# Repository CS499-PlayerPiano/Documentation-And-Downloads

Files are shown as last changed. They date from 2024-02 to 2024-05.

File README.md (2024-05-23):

# Documentation and Downloads
Here you will find misc files and documentation for the piano.

- [Documentation and Downloads](#documentation-and-downloads)
  - [Presentation & Writeup](#presentation--writeup)
  - [3D Models](#3d-models)
  - [Electronics \& Schematics](#electronics--schematics)
  - [Code and Runtime](#code-and-runtime)

## [Presentation & Writeup](./Presentation%20and%20Writeup/)
This folder contains the presentations and writeups for our projects.
* [Final Presentation Video](https://www.youtube.com/watch?v=wYrI8wo7iek)
* [Final Writeup (PDF)](./Presentation%20and%20Writeup/Player%20Piano%20Final%20Report.pdf)
* [Presentation (PDF)](./Presentation%20and%20Writeup/Player%20Piano.pdf)
* [Presentation (PPTX)](./Presentation%20and%20Writeup/Player%20Piano.pptx)

## [3D Models](./3D%20Models/README.md)
This folder contains the 3D models for the piano. The models are in `.stl` format and can be viewed in any 3D modeling software. There are also `.f3z` files which are the original files for the 3D models in the Fusion 360 software.

## [Electronics & Schematics](./Electronics%20and%20Schematics/README.md)
This folder contains the schematics for the piano, and the PCB design files.
* [V1.0](./Electronics%20and%20Schematics/v1.0/)
* [V1.1](./Electronics%20and%20Schematics/v1.1/)

## [Code and Runtime](./Code%20and%20Runtime/)
This folder contains info how to run and configure the various programs that run the piano.
* [Running the piano program(s)](./Code%20and%20Runtime/Running.md)
* [Configuration](./Code%20and%20Runtime/Configuration.md)

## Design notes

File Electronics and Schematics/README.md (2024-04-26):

# Electronic and Schematics
This folder contains the schematics for the piano, and the PCB design files.

- [Electronic and Schematics](#electronic-and-schematics)
  - [Schematic and PCB Design](#schematic-and-pcb-design)
    - [Version 1.0](#version-10)
    - [Version 1.1](#version-11)

## Schematic and PCB Design
### Version 1.0
* [EasyEDA Schematic](./v1.0/SCH_PLU-Piano-v1.0_2024-04-26.json)
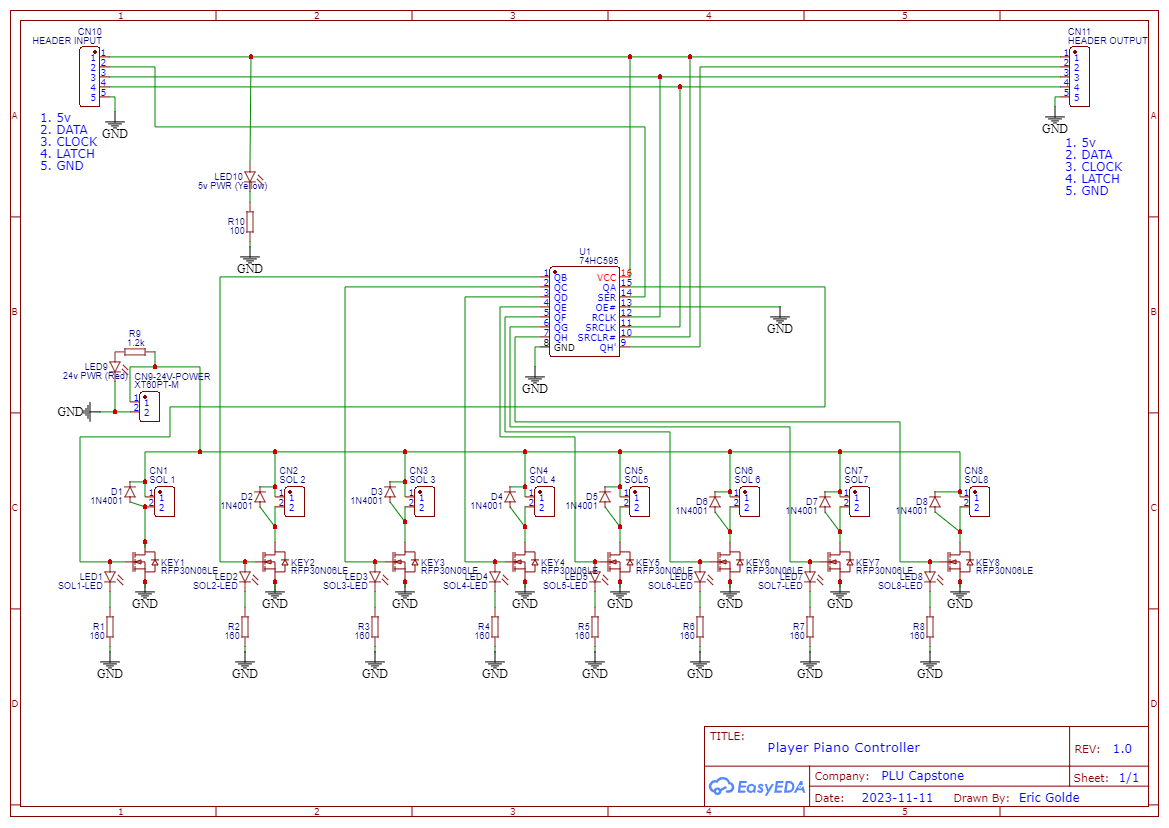
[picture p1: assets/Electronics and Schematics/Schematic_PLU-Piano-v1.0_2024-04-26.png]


* [Gerber Files](./v1.0/Gerber_PLU-Piano-v1.0_PCB_PLU-Piano-v1.0_2024-04-26.zip)
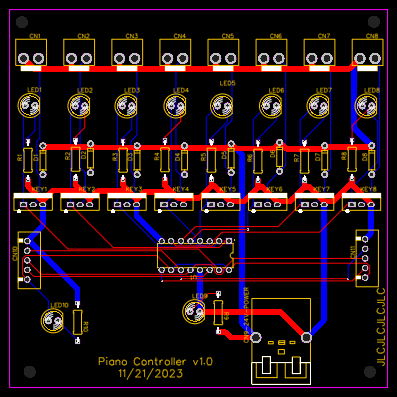
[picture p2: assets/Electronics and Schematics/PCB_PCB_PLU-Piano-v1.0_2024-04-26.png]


* [BOM](./v1.0/BOM_PLU-Piano-v1.0_2024-04-26.csv)

### Version 1.1
* [EasyEDA Schematic](./v1.1/SCH_PLU-Piano-v1.1_2024-04-26.json)
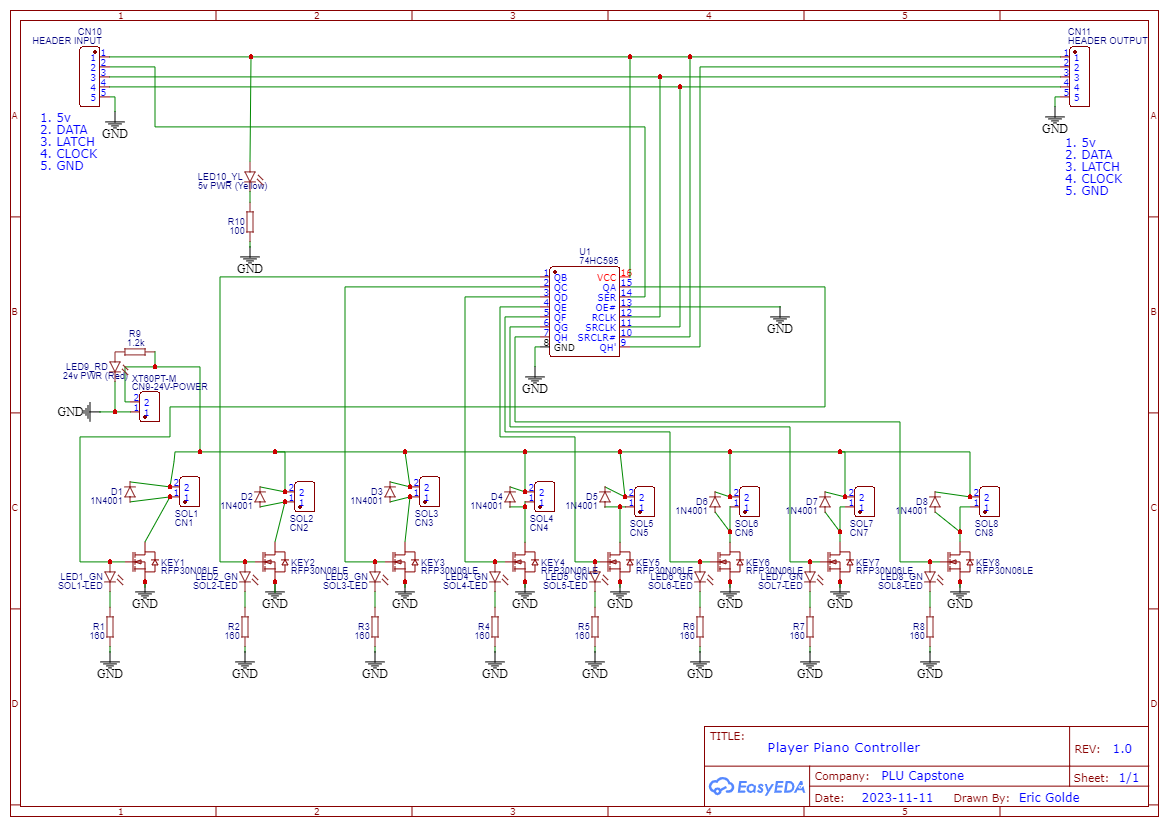
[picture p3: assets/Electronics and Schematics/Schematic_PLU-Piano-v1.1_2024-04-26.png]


* [Gerber Files](./v1.1/Gerber_PLU-Piano-v1.1_PCB_PLU-Piano-v1.1_2024-04-26.zip)
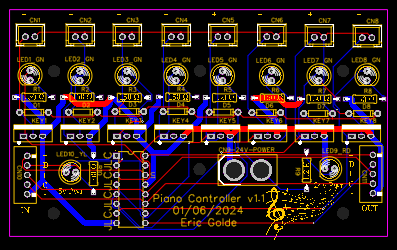
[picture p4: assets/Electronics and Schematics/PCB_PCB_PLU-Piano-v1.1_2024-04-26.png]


* [BOM](./v1.1/BOM_PLU-Piano-v1.1_2024-04-26.csv)

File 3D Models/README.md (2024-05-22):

## 3D Models
### [Solenoid Holder](./Solenoid%20holder/)
Settings:
- Perimeters: 6
- Infill: 25%
- 0.2mm layer height
- PETG

Files:
- [SolenoidHolder2 v13.f3d](./Solenoid%20holder/SolenoidHolder2%20v13.f3d) - Main tileable solenoid holder
- [SolenoidHolder2 v13.stl](./Solenoid%20holder/SolenoidHolder2%20v13.stl) Main tileable solenoid holder
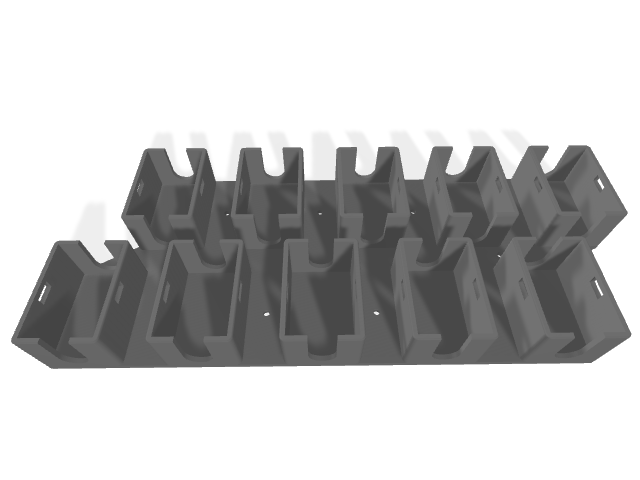
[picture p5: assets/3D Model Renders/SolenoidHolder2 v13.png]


- [LeftWhiteKeyFrame.stl](./Solenoid%20holder/LeftWhiteKeyFrame.stl) - 7 keys for the left end
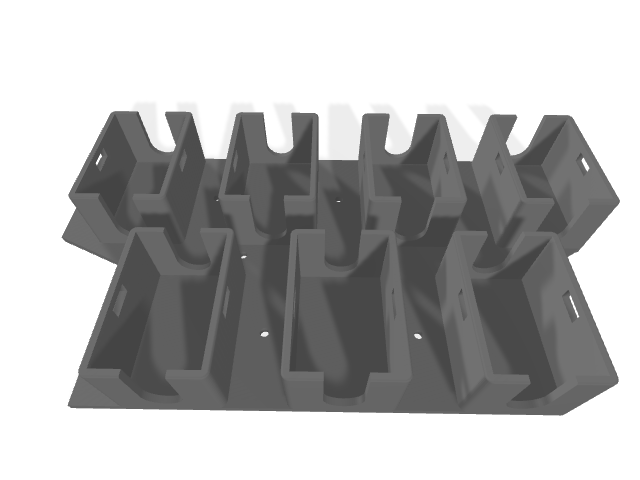
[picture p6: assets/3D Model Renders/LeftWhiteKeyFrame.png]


- [RightWhiteKeyFrame.stl](/Solenoid%20holder/RightWhiteKeyFrame.stl) - 5 keys for the right end
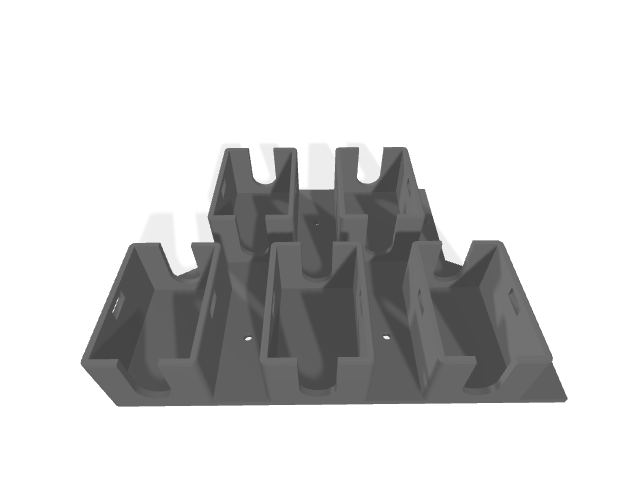
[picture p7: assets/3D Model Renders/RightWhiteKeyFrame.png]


### [Threaded Rod Connectors](./Threaded%20Rod%20Connectors/)
Settings:
- Perimeters: 3
- Infill: 25%
- 0.2mm layer height
- PETG

Files:
- [ThreadedRodConnectors v12.f3d](./Threaded%20Rod%20Connectors/ThreadedRodConnectors%20v12.f3d) - Connects the solenoid to the threaded rod
- [SolenoidToRodAttachment.stl](./Threaded%20Rod%20Connectors/SolenoidToRodAttachment.stl) - Connects the solenoid to the threaded rod
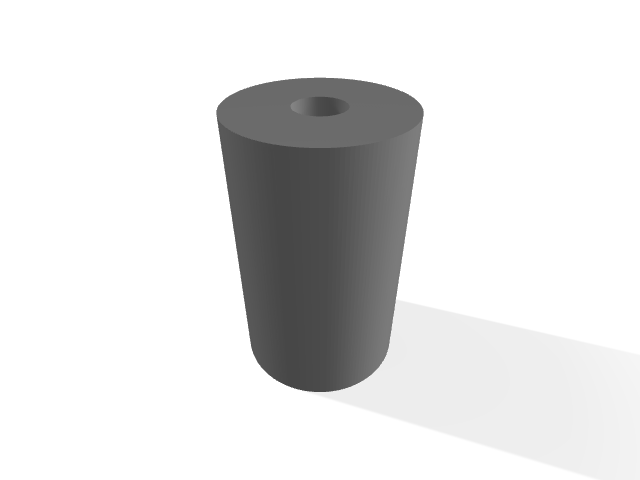
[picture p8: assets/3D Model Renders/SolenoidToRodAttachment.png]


- [Striker](./Threaded%20Rod%20Connectors/Striker.stl) - Connects the threaded rod to hit the keys
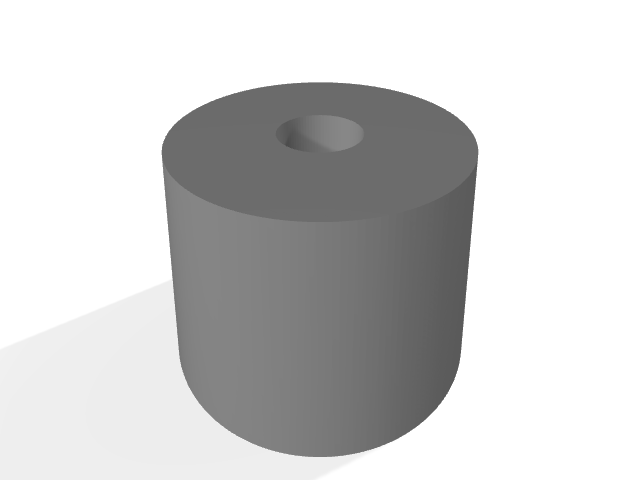
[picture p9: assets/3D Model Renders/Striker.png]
Striker


- [Power Strip Bracket](./PowerStripBracket.stl)
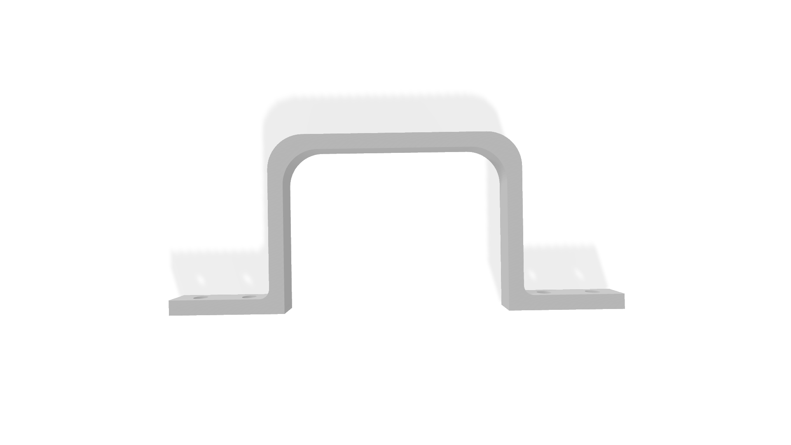
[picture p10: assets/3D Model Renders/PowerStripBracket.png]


- [Power Supply Mount](./Power%20Supply/)
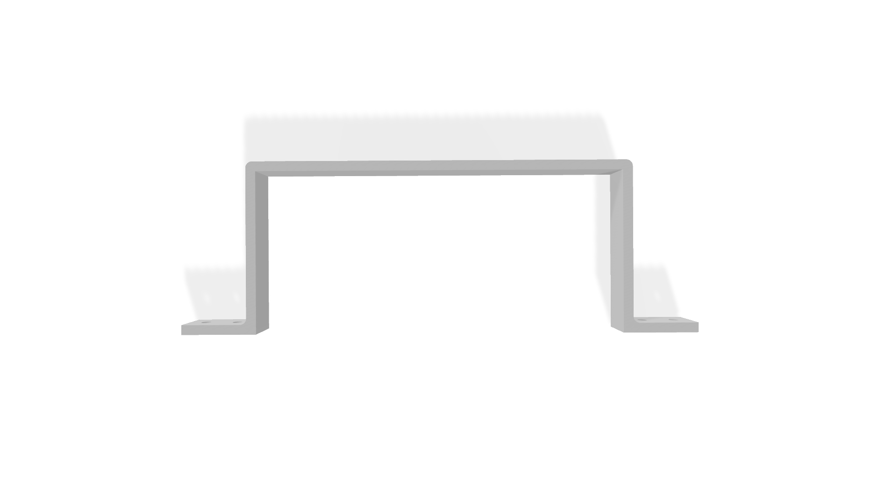
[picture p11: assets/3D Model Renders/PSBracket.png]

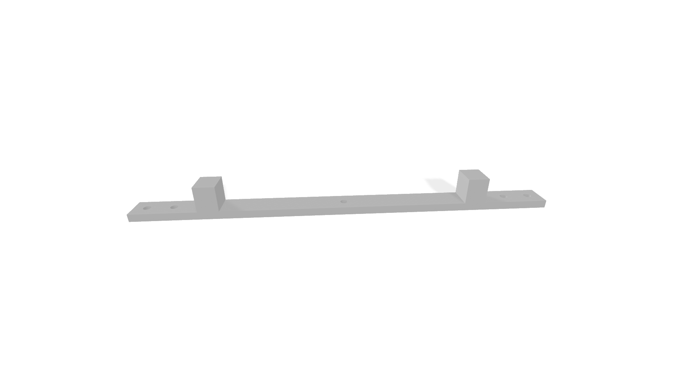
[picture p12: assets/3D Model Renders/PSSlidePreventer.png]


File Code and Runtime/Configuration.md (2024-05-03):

# Configuration

## Outputs.json
```json5
{
    // Configuration for the Logger output
    "Logger": {
        "enabled": true
    },

    // Configuration for the Midi Synthesizer
    "Midi Synthesizer": {
        "enabled": true
    },

    // Configuration for the Virtual Piano GUI
    "Virtual Piano GUI": {
        "enabled": true,

        // Either "RAINBOW_GRADIENT" or "TRACK_NUMBER"
        "colorMode": "RAINBOW_GRADIENT"
    },

    // Configuration for the Synthesia Viewer (Not yet implemented)
    "Synthesia Viewer": {
        "enabled": false
    },

    // Configuration for the web server
    "Javalin Web Server": {

        // Port to run the web server on
        "port": 8898,

        // Interval in milliseconds to send timestamp updates to the client
        "timestampInterval": 500
    },

    // Configuration for the Physical Piano
    "Arduino": {
        "enabled": true,

        // COM port for the Arduino
        "comPort": "COM7",

        // Baud rate for the Arduino
        "baudRate": 115200,

        // Should we print debug output if the Arduino sends it?
        "printDebugOutputFromArduino": true,

        // Should we send a power reset after every song?
        "sendPowerResetAfterEverySong": true,

        // Shoud we ignore velocity, and only send 255 or 0?
        "ignoreVelocity": false,

        // Velocity mapping for energising the solenoids.
        // The solenoids stop responding at 120, and are fully energised at 255.
        "velocityMapping": {
            "min": 120,
            "max": 255
        },

        // Mapping of the notes to the solenoids
        // Physical Key Index -> Midi Note
        // 0 is the lowest key, 87 is the highest key
        "noteMapping": {
            "0": 101,
            "1": 102,
            "2": 103,
            "3": 104,
            "4": 105,
            "5": 106,
            "6": 107,
            "7": 108,
            "8": 93,
            "9": 94,
            "10": 95,
            "11": 96,
            "12": 97,
            "13": 98,
            "14": 99,
            "15": 100,
            "16": 85,
            "17": 86,
            "18": 87,
            "19": 88,
            "20": 89,
            "21": 90,
            "22": 91,
            "23": 92,
            "24": 77,
            "25": 78,
            "26": 79,
            "27": 80,
            "28": 81,
            "29": 82,
            "30": 83,
            "31": 84,
            "32": 69,
            "33": 70,
            "34": 71,
            "35": 72,
            "36": 73,
            "37": 74,
            "38": 75,
            "39": 76,
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
        }
    }
}
```

## Programs.json
```json5
{
    // Configuration for the Midi Keyboard Input
    "midi-keyboard": {
        // Should we print all the device names on boot?
        "printAllDeviceNames": true,

        // Name of the device to use
        "deviceName": "AKM320",

        // Should we ignore velocity when reading the midi input?
        "ignoreVelocity": true
    }
}
```

## TODO Configs:
We ran out of time to make these configurable, but they should be configurable in the future.
```
plu.capstone.playerpiano.sheetmusic.cleaner.steps.Step4OffsetNoteTimes LN: 28-120. timeToRelease(), timeToHit(), calcShiftForwardAmount()
```

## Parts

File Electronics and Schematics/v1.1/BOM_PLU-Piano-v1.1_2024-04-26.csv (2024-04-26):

ID | Name | Designator | Footprint | Quantity | Manufacturer Part | Manufacturer | Supplier | Supplier Part | Price | Pins | 3DModel | Contributor | JLCPCB Part Class | description | link
1 | 24v PWR (Red) | LED9_RD | LED5MM | 1 |  |  |  |  |  | 2 | LED-TH-5MM_RED COPY | SparkFun
2 | SOL1-LED | LED1_GN | LED5MM | 1 |  |  |  |  |  | 2 | LED-TH-5MM_G COPY | SparkFun
3 | SOL2-LED | LED2_GN | LED5MM | 1 |  |  |  |  |  | 2 | LED-TH-5MM_G COPY | SparkFun
4 | SOL3-LED | LED3_GN | LED5MM | 1 |  |  |  |  |  | 2 | LED-TH-5MM_G COPY | SparkFun
5 | SOL4-LED | LED4_GN | LED5MM | 1 |  |  |  |  |  | 2 | LED-TH-5MM_G COPY | SparkFun
6 | SOL5-LED | LED5_GN | LED5MM | 1 |  |  |  |  |  | 2 | LED-TH-5MM_G COPY | SparkFun
7 | SOL6-LED | LED6_GN | LED5MM | 1 |  |  |  |  |  | 2 | LED-TH-5MM_G COPY | SparkFun
8 | SOL7-LED | LED7_GN | LED5MM | 1 |  |  |  |  |  | 2 | LED-TH-5MM_G COPY | SparkFun
9 | SOL8-LED | LED8_GN | LED5MM | 1 |  |  |  |  |  | 2 | LED-TH-5MM_G COPY | SparkFun
10 | 5v PWR (Yellow) | LED10_YL | LED5MM | 1 |  |  |  |  |  | 2 | LED-TH_5MM_YELLOW-GREEN | SparkFun
11 | SOL1 | CN1 | CONN-TH_XH-2A | 1 | XH-2A | 韩国韩荣 | LCSC | C2910525 | 0.043 | 2 | XH2.5-2A | LCSC | Extended Part |  | https://item.szlcsc.com/20789.html
12 | SOL2 | CN2 | CONN-TH_XH-2A | 1 | XH-2A | 韩国韩荣 | LCSC | C2910525 | 0.043 | 2 | XH2.5-2A | LCSC | Extended Part |  | https://item.szlcsc.com/20789.html
13 | SOL3 | CN3 | CONN-TH_XH-2A | 1 | XH-2A | 韩国韩荣 | LCSC | C2910525 | 0.043 | 2 | XH2.5-2A | LCSC | Extended Part |  | https://item.szlcsc.com/20789.html
14 | SOL4 | CN4 | CONN-TH_XH-2A | 1 | XH-2A | 韩国韩荣 | LCSC | C2910525 | 0.043 | 2 | XH2.5-2A | LCSC | Extended Part |  | https://item.szlcsc.com/20789.html
15 | SOL5 | CN5 | CONN-TH_XH-2A | 1 | XH-2A | 韩国韩荣 | LCSC | C2910525 | 0.043 | 2 | XH2.5-2A | LCSC | Extended Part |  | https://item.szlcsc.com/20789.html
16 | SOL6 | CN6 | CONN-TH_XH-2A | 1 | XH-2A | 韩国韩荣 | LCSC | C2910525 | 0.043 | 2 | XH2.5-2A | LCSC | Extended Part |  | https://item.szlcsc.com/20789.html
17 | SOL7 | CN7 | CONN-TH_XH-2A | 1 | XH-2A | 韩国韩荣 | LCSC | C2910525 | 0.043 | 2 | XH2.5-2A | LCSC | Extended Part |  | https://item.szlcsc.com/20789.html
18 | SOL8 | CN8 | CONN-TH_XH-2A | 1 | XH-2A | 韩国韩荣 | LCSC | C2910525 | 0.043 | 2 | XH2.5-2A | LCSC | Extended Part |  | https://item.szlcsc.com/20789.html
19 | XT60PT-M | CN9-24V-POWER | CONN-TH_XT60 | 1 | XT60PT-M | AMASS(艾迈斯) | LCSC | C98733 | 0.181 | 2 | CONN-TH_XT60 | lcsc |  |  | https://lcsc.com/eda_search?q=C5155958&%26type=1&ref=editor
20 | RFP30N06LE | KEY1,KEY2,KEY3,KEY4,KEY5,KEY6,KEY7,KEY8 | TO-220AB-3_L10.3-W4.5-P2.54-L-1 | 8 | RFP30N06LE-VB | VBsemi(微碧) | LCSC | C878812 | 0.504 | 3 | TO-220AB-3_L10.3-W4.5-P2.54-L-1 | LCSC | Extended Part |  | https://lcsc.com/eda_search?q=C878812&%26type=1&ref=editor
21 | 74HC595 | U1 | PDIP-16_L19.7-W6.6-P2.54-LS7.6-BL | 1 | SN74HC595NE4 | TI(德州仪器) | LCSC | C3303991 | 0.337 | 16 | PDIP-16_L19.7-W6.6-H5.1-P2.54-LS7.6-BL | lcsc |  |  | https://lcsc.com/eda_search?q=C3303991&%26type=1&ref=editor
22 | 160 | R1,R2,R3,R4,R5,R6,R7,R8 | RTH025W | 8 |  |  |  |  |  | 2 | 150Ohm-T-07-5 | DangerousPrototype
23 | 1.2k | R9 | RTH025W | 1 |  |  | Mouser |  |  | 2 | 1.2K 0.25W | DangerousPrototype
24 | 100 | R10 | RTH025W | 1 |  |  |  |  |  | 2 | R100 Ohm | DangerousPrototype
25 | 1N4001 | D1 | DIODE-1N4148 | 1 |  |  |  |  |  | 2 | DIODE-THL-3D-1N4148-L10.5 COPY | SparkFun |  | Diode
26 | 1N4001 | D2,D3,D4,D5,D6,D7,D8 | DIODE-1N4148 | 7 |  |  |  |  |  | 2 |  | SparkFun |  | Diode
27 | HEADER INPUT | CN10 | CONN-TH_HEADER5 | 1 | Header5 | null | LCSC | C9900003337 |  | 5 | CONN-TH_HEADER5 | LCSC | Extended Part |  | https://lcsc.com/eda_search?q=C9900003337&%26type=1&ref=editor
28 | HEADER OUTPUT | CN11 | CONN-TH_HEADER5 | 1 | Header5 | null | LCSC | C9900003337 |  | 5 | CONN-TH_HEADER5 | LCSC | Extended Part |  | https://lcsc.com/eda_search?q=C9900003337&%26type=1&ref=editor

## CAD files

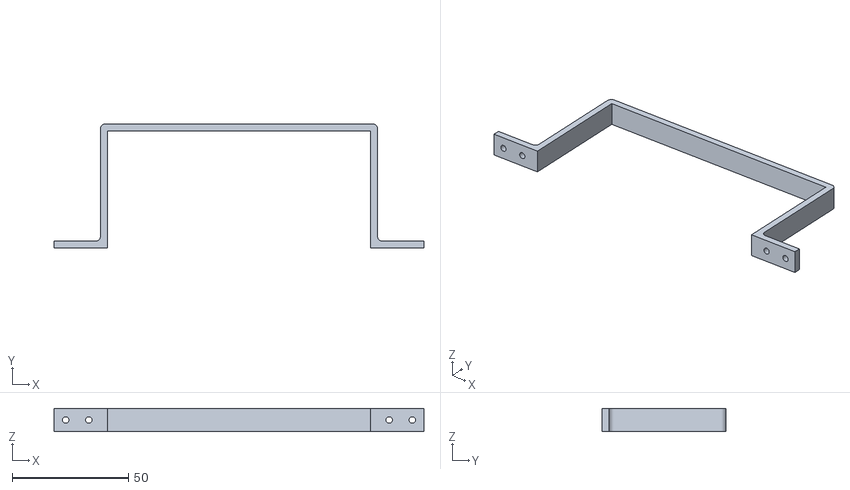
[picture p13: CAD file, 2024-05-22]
3D Models/Power Supply/PSBracket.stl
159.4 x 53.4 x 10.0

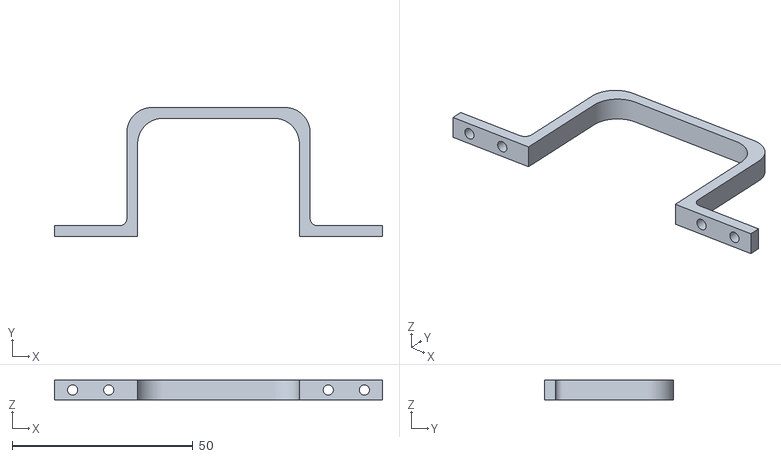
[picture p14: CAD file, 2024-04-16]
3D Models/PowerStripBracket.stl
90.7 x 35.7 x 5.50

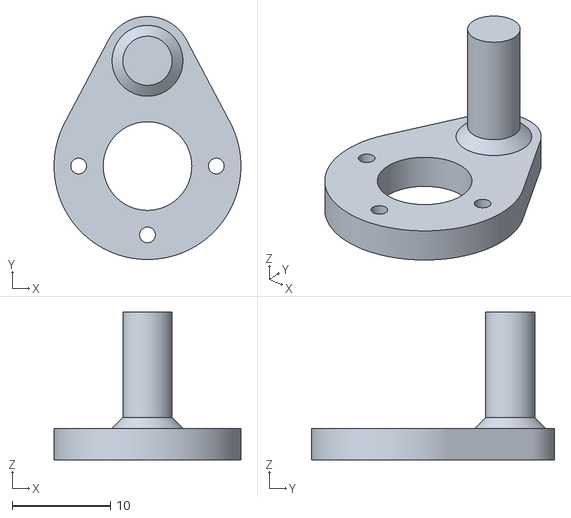
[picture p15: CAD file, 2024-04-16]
3D Models/Servo Mount/ServoArm.stl
19.0 x 24.7 x 15.0

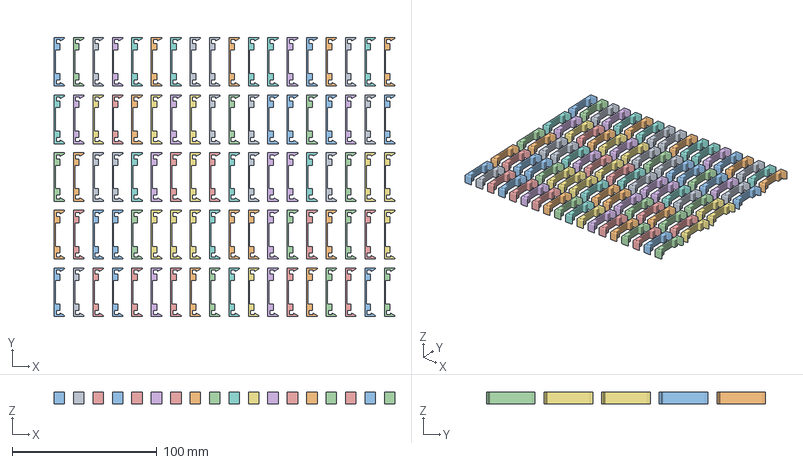
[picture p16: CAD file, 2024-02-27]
3D Models/Solenoid holder/90Clip.3mf
235.5 x 193.0 x 7.95 mm
Clip.stl x 90

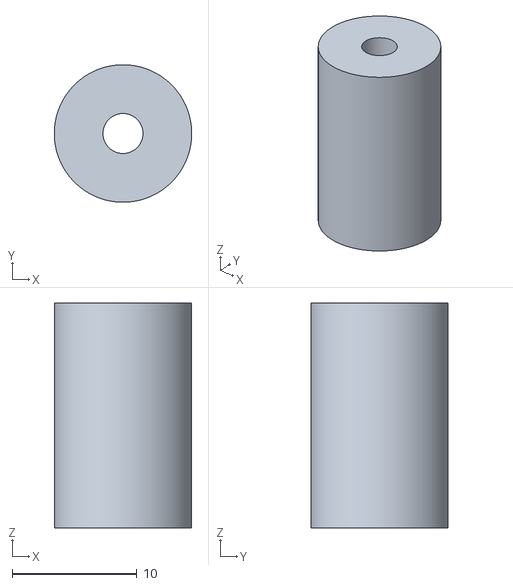
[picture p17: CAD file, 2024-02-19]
3D Models/Threaded Rod Connectors/SolenoidToRodAttachment.stl
11.0 x 11.0 x 18.0

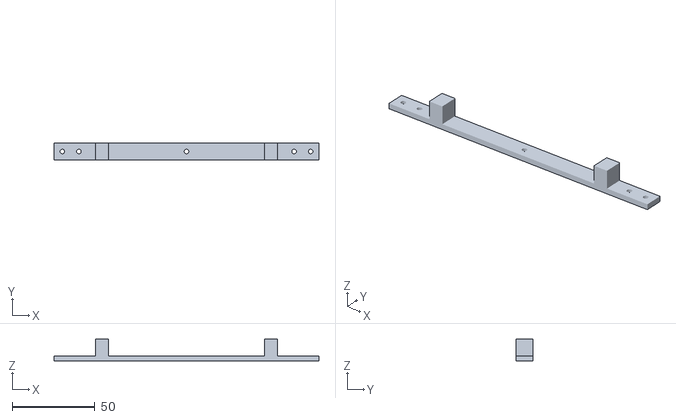
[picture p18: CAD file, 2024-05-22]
3D Models/Power Supply/PSSlidePreventer.stl
160.0 x 10.0 x 13.0

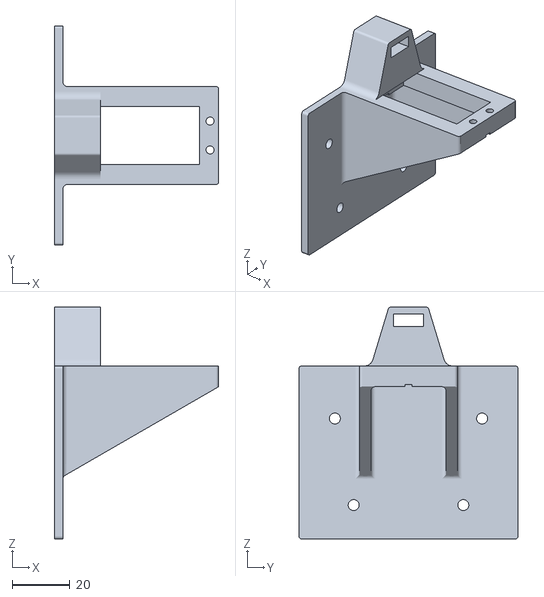
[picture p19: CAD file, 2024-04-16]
3D Models/Servo Mount/ServoMount.stl
57.0 x 76.0 x 80.4

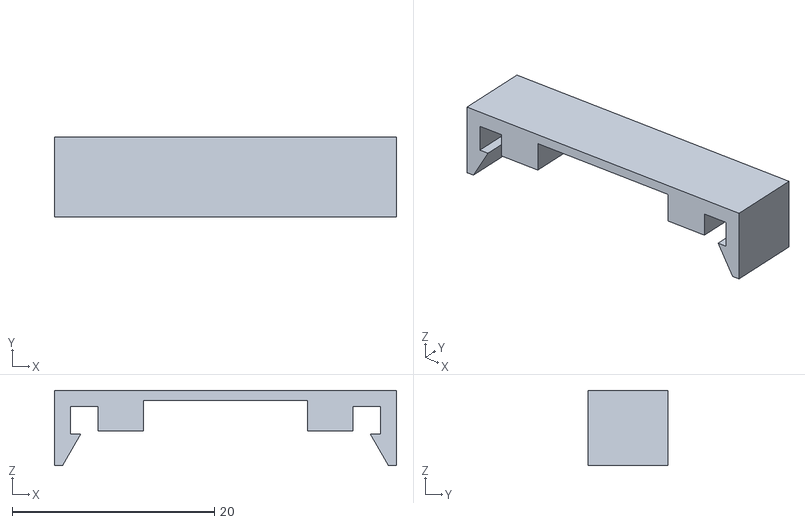
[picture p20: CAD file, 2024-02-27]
3D Models/Solenoid holder/Clip.stl
33.8 x 7.95 x 7.42

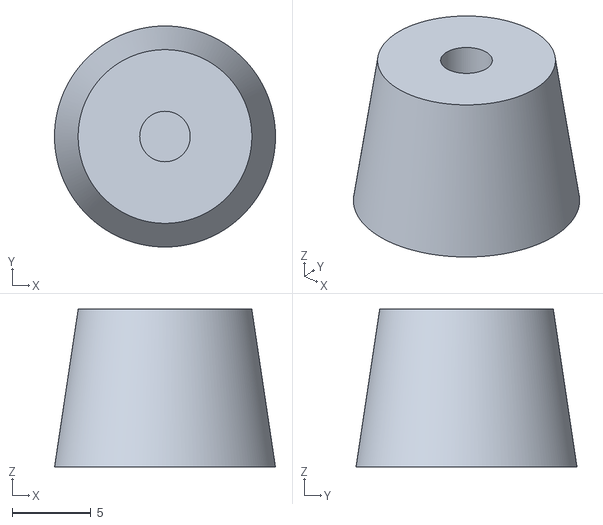
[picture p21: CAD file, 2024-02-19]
3D Models/Threaded Rod Connectors/Striker.stl
14.0 x 14.0 x 10.0

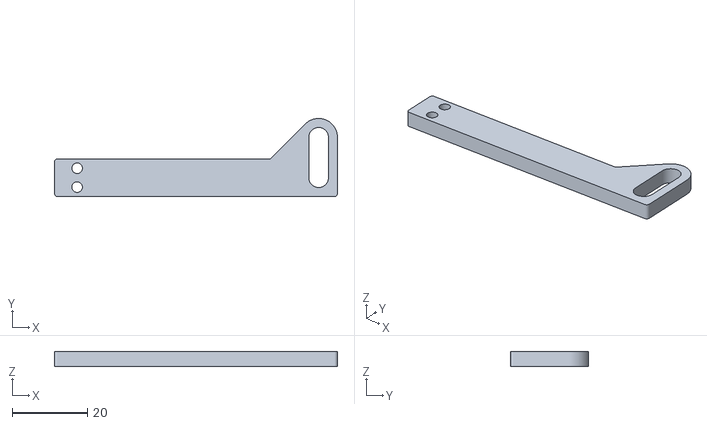
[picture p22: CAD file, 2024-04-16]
3D Models/Servo Mount/Slider.stl
75.0 x 20.7 x 4.00

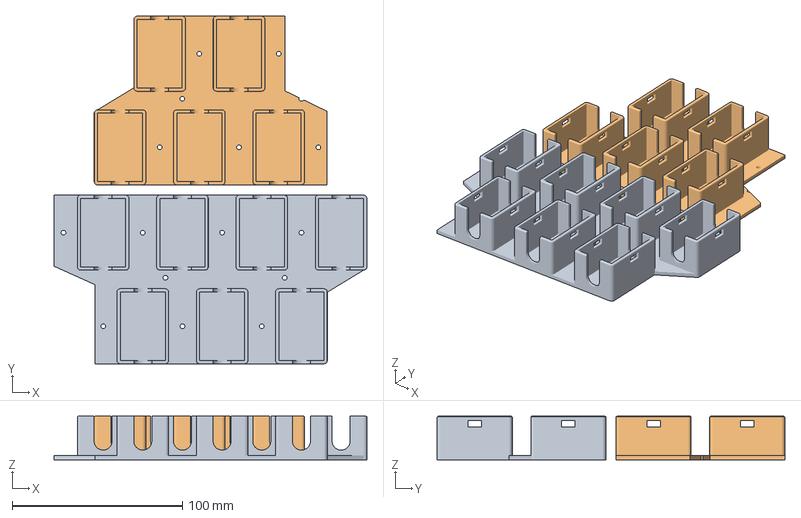
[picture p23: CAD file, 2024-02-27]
3D Models/Solenoid holder/LeftRightWhiteKeyFrame.3mf
183.9 x 204.2 x 25.6 mm
LeftWhiteKeyFrame.stl
RightWhiteKeyFrame.stl

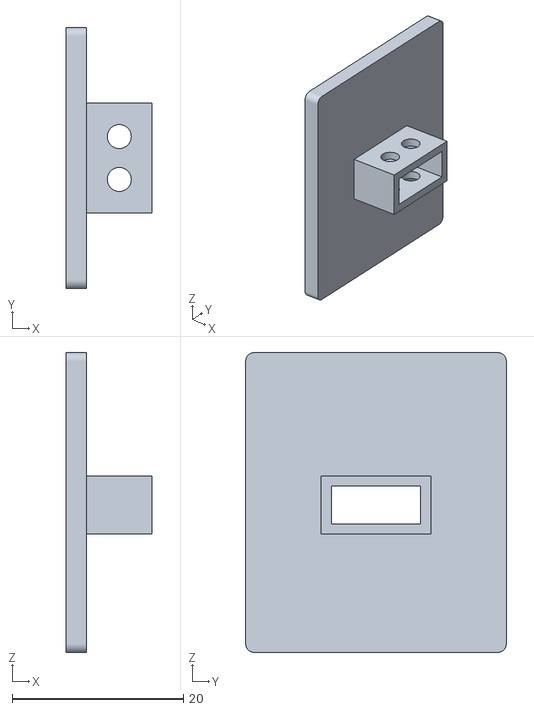
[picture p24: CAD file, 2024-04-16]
3D Models/Servo Mount/PushingSurface.stl
10.0 x 30.4 x 35.0

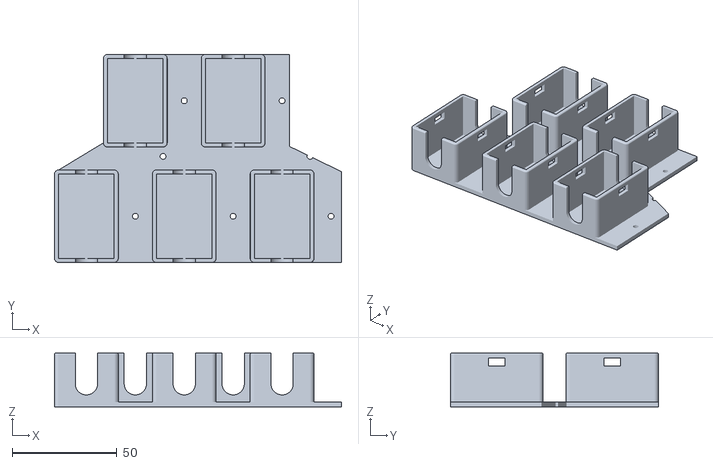
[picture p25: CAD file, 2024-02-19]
3D Models/Solenoid holder/RightWhiteKeyFrame.stl
136.7 x 99.1 x 25.6

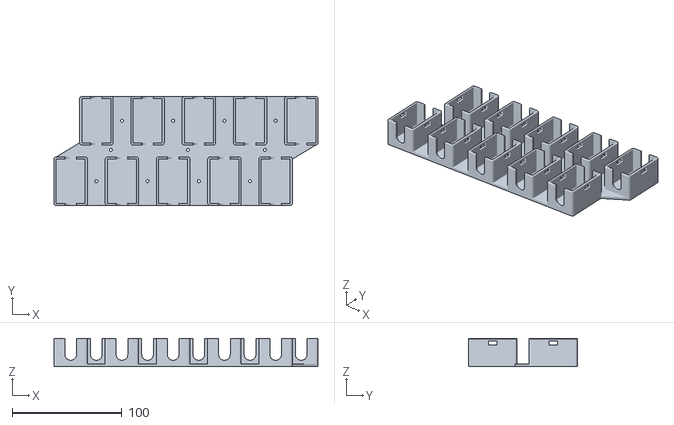
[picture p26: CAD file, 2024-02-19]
3D Models/Solenoid holder/SolenoidHolder2 v13.stl
240.1 x 99.1 x 25.6

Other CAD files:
3D Models/Solenoid holder/LeftWhiteKeyFrame.stl
3D Models/Servo Mount/PedalServo v8.f3z
3D Models/Solenoid holder/SolenoidHolder2 v13.f3d
3D Models/Threaded Rod Connectors/ThreadedRodConnectors v12.f3d

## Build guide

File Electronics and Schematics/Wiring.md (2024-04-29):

# Piano Wiring

## Schematic
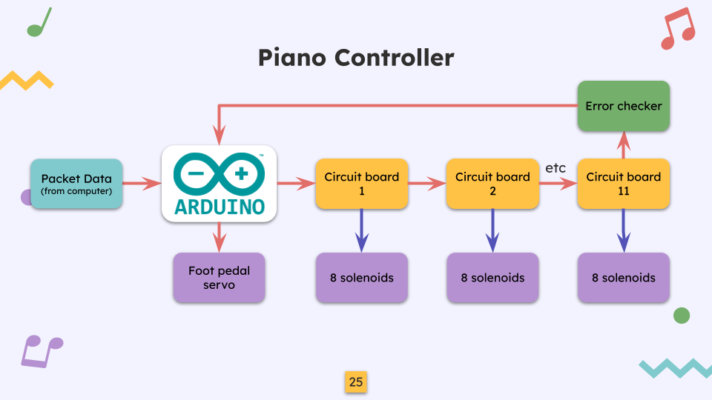
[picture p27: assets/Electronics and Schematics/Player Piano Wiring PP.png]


## Pins
| Pin | Arduino Name| Function |
| --- | --- | --- |
| 2 | DATA | Data line for the shift register boards |
| 3 | CLOCK | Clock line for the shift register boards |
| 4 | LATCH | Latch line for the shift register boards |
| 5| RELAY | Relay to reset 5v line |
| 6 | SERVO | Servo motor for the sustain pedal |
| 7 | CHECKBIT | Check bit return from the error checker board |

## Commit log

2024-02-19 Commit of 3d models and basic readme
    [LeftWhiteKeyFrame.stl, RightWhiteKeyFrame.stl, SolenoidHolder2 v13.f3d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]
2024-02-27 Added few more exported stls. Need documentation
    [90Clip.3mf, Clip.stl, LeftRightWhiteKeyFrame.3mf]
2024-04-16 Added a few more 3d models
    [PedalServo v8.f3z, PowerStripBracket.stl, PushingSurface.stl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]
2024-04-26 Added schematics and runtime instructions
    [BOM_PLU-Piano-v1.0_2024-04-26.csv, BOM_PLU-Piano-v1.1_2024-04-26.csv]
2024-04-29 Added wiring image
2024-05-16 Added Powerpoint
2024-05-22 Added rest of 3D models
    [PSBracket.stl, PSSlidePreventer.stl, PowerStripBracket.stl]
